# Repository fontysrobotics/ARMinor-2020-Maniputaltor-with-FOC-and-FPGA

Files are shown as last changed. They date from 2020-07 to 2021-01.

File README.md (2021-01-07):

# Affordable Manipulator With FPGA-driven FOC 

### Introduction 

Robotics can be prohibitively expensive and complex, preventing robotics students from learning about them. The goal of this project was to design an affordable, easy to use robot arm that would help solve these problems. The project was split into four parts: the electrical design, the mechanical design, the Field Oriented Control (FOC) implementation, and the simulation. Each of these projects' parts will be discussed in order below.

**This repository supports trainings at the ROS-Industrial training centre at Fontys University of Applied Sciences for the Adaptive Robotics minor ([ROSIN EP FREROS project](https://www.rosin-project.eu/ftp/freros))**

**This Educational Project has received funding from the European Union's Horizon 2020 research and innovation programme under the project ROSIN with the grant agreement No 732287.**



### Project structure

- **Electrical Design:** Within this folder you will find schematics, hardware documentation that was selected for the affordable manipulator.

- **Mechanical Design:** Within this folder you will find the proof of concept of the manipulator's mechanical design, alongside some design hardware selection documentation.

- **FieldOrientedControl:** Within this folder you will find the FOC implementation within FPGA boards. The files there is a simulink model of the controller and motors.

- **Simulation:** Within this folder you will find the simulation of the affordable manipulator in Unity. The project files for the communication between ROS and Unity, and the proof of concept of an GUI to interface with the simulation. 

**There is a final report available in this repository, which is meant to be the compiled version of our results and findings**

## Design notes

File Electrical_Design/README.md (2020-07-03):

# Electrical Design
## General information 
The robotic arm will have 6 axes with a 100W 3-phase ac motor in each. 
It has to have a tool interface at its end with a 24V power supply and 24V I/O pins.
The robotic arm should be able to be plugged into the 230V 50Hz mains. 

## Power supplies
For the main power supplies a MEAN WELL RSP-750-48 and a MEAN WELL RS-35-5 were chosen for the 48V and 5V lines respectively.
They fit all the requirements for safety features and the RSP-750-48 also has active power factor correction.
It can continuously deliver 750 W and has active cooling.
Thus, it would be able to power the motor drivers for extended periods of time. 
Unfortunately, something that cannot be remotely tested or calculated is how well it behaves with the transient load of the motors. 

The low voltage power supply can deliver up to 35W, which would be enough for all the systems that use 5V or less. Moreover, those systems do not cause the same problems with transient loads so the power supply will handle it well.

It should be physically tested whether the power supply witll be able to handle the transient load of the 6 motors turning on or off at once. 

## FPGA 
Because each motor controller board has an individual FPGA, an FPGA with less pins and less logic gates could be chosen.
The Spartan-3A Xilinx XC3S50A-4VQG100C (Xilinx) was a suitable choice because of multiple reasons.
Fist it got a suitable price for the goal.
It also has a package with pins on the side instead of a ball grid array.
This makes it much easier to solder it by hand, which is helpful for this in-house project.
Moreover, it is from Xilinx, which was already used previously in the minor, thus the students were already familiar with its software. 

## Tool power supply 
The tool power supply is a simple implementation of a Buck convertert that steps down the 48V for the power supply to 24V.
The design goal was to be able to provide at least 600mA current, but this one can go to over 1A.

## The schematic 
The schematic was done on the free version of Eagle 9.1.3. It was not build and physically tested.
Because of the corona outbreak it was not possible to go to Fontys and build or test anything physical.
Therefore it is reccommended that the schematic is first built on a prototype board and tested carefully. 

## Communication between the main controller and motor controllers
In order to minimize the amount of cables inside the robot arm the motor drivers will be inside the axes, next to the motors and the main controller will communicate with them through the I2C protocol.
In this way there will be only 5 cables that run through the arm, moreover the signal will be more noise proof compared to the situation where the motor drivers will be inside the base and the connection from them to the motors will run through the robot arm. 
The tool I/O will also be controlled through the I2C lines.
This is possible since the tool does not require a big I/O bandwidth and the I2C standard bandwidth will be fast enough to accommodate both all of the motor controllers and the tool I/O as well.

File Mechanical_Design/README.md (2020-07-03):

# Mechanical Design
For the mechanical design, there were two main parts that were considered:

The manipulator frame:

Aluminium extrusion was hosen for the frame, as this is lightweight, easy to acquire and assemble, and allows for the cables to be hidden.

The manipulator joints:

For the manipulator joints, pre-built joints were found.
These allow minimisation of cost and omplexity, while achieving high performance.

For more details on the components selected and he recommendations, please see the project report.

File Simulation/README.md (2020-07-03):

# Simulation

### Within this folder you will find two different project folders
- **GUI**: UR like interface proof on concept designed to interface with the simulation 
- **Simulation:** Robotic arm simulation in Unity

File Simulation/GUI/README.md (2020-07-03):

# ManArm Controller
## Description
This is a controller for a robot that had to be built during an Adaptive Robotics minor
at Fontys University of Applied Sciences.

Goals: 
* Provide a control interface similar to other robot arms on the market
* Support Linux including ARM, optionally windows  
* Save and load robot programs between platforms
* Control of each individual joint and IO pins

This project uses Tkinter as it supports different architectures. This toolkit is beginner friendly 
but also offers advanced features. 

## How to start
In order to start the UI you need to start the main_window.py with python 2. 

`` python src/gui/main_window.py ``

To run the guy you need to have `pillow` and `rospy` installed. You can install pillow by running.
`` pip install pillow ``

To install rospy please refer to installation of ROS. 

To run the unity simulation refer to the Simulation folder in this repository.

## Work in progress
This project is still in the early stage of development.

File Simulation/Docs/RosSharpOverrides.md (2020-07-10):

RosSharp Asset override list
======

| File | Changes |
|---|---|
| __Joint overrides__ | base joint management |
| `UrdfJoint` | Allowed the `Start()` function to be overridden |
| `UrdfJointRevolute` | - Added an encoder type system to track the angle of the joint as the build-in angle reporting is not always correct. <br /> - Added methods for motor control (velocity and effort control) |
| __Ros bridging__ | Overrides in message handling |
| `JointStateReader` | - Added calibration system so the zero angle can be changed / properly set. <br /> - Added normalization so values are between -180 and 180 degrees |

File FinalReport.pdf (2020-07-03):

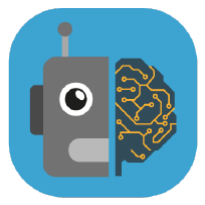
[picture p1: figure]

Fontys University of Applied Sciences

# Affordable Manipulator With FPGA-driven FOC

Final progress report

7-1-2020

Limpens, Jordie J.J.N.
Marinov, Mihail M.M.
Mindiola Romero, Ray R.D.
Sminia, Sean, S.M.
Strik, Leonardo L.S.

I
Affordable Manipulator With FPGA-driven FOC - Preface

## Preface

This document is the final report of a project about the design of an affordable 6 degree of freedom manipulator arm, which was part of the Adaptive Robotics minor at Fontys University of Applied Sciences. The goal of the project was to design an affordable robot arm, that could be used for educational purposes. It was motivated by the fact that currently available robot manipulators are expensive and although Fontys has a few, close to project deadlines the demand for them is too big. An affordable, in-house produced manipulator arm would not only help meet the student’s demand, but, since students will have access to the design documents and source code, will also allow them to improve it and modify it while studying robotics.

The project was worked on in the period from March 2020 until June 2020. Unfortunately, the project coincided with a global pandemic, which caused all work on the project to be remote, thus nothing could be physically made nor tested. This limitation has shifted the initially planned goals and end product of the project. Despite the difficult period, the group has put effort in order to finish as much as possible in order to provide a solid groundwork for the completion of
the initially intended product.

The group members would like to express significant appreciation to Peter Klijn, who was our tutor for this project and helped us greatly. We also are thankful to Pablo Negrete, who created the project, gave us tips and acted as a client for the project’s purposes. We are thankful for the advice given by Esmaeil Najafi, which was also very helpful for our project. Lastly, we also wish to acknowledge the help provided by Edwin Insuasty from MathWorks with modelling and designing the motor controllers of the robot arm.

This report is mainly intended for the students who will continue working on this project, as well as the teachers who will assess our work. The document is divided into different chapters for different fields of engineering in order to facilitate finding the information that the reader is seeking. In the end recommendations for further development are listed.

II
Affordable Manipulator With FPGA-driven FOC - Contact details

## Contact details

Below, the contact details for all group members, the client, and the tutor are presented.

### Group members:

Name | Student number | Email | Phone number
Ray Mindiola | 2588005 | r.mindiolaromero@student.fontys.nl | +31 6 49 674 116
Sean Sminia | 2718383 | s.sminia@student.fontys.nl | +31 6 29 027 316
Leonardo Strik | 2909332 | l.leonardo@student.fontys.nl | +31 6 36 348 027
Mihail Marinov | 3225666 | m.marinov@student.fontys.nl | +31 6 40 901 311
Jordie Limpens | 3312976 | j.limpens@student.fontys.nl | +31 6 27 122 022

### Client:

Name | Pablo Negrete Rubio
Email | p.negreterubio@fontys.nl
Phone number | 0885074731

### Tutor:

Name | Peter Klijn
Email | p.klijn@fontys.nl
Phone Number | 0885070657

III
Affordable Manipulator With FPGA-driven FOC - Summary

## Summary

Robotics can be prohibitively expensive and complex, preventing robotics students from learning about them. The goal of this project was to design an affordable, easy to use robot arm that would help solve these problems. The project was split into four parts: the electrical design, the mechanical design, the Field Oriented Control (FOC) implementation, and the simulation. Each of these projects' parts will be discussed in order below. For the electoral design, there were three main decisions: Using two different power supplies, a low and high voltage one, to eliminate interplay , the use of separate FPGA drivers for each motor, to minimize interference and cables through the arm, and the application of the I2C protocol to communicate sensor and motor data. In regard to the mechanical design, there were two important decisions: The use of aluminium extrusion, to minimize weight and complexity, and the application of pre-built joints, to minimise cost and complexity. The FOC implementation within Simulink and the exported VHDL code seemed to behave accordingly, although sufficient testing lacked due to time constraints. In order to minimize complexity and cost, pre-configured full system kits were chosen for the FOC solution. In regard to the simulation, Unity was chosen as a simulator. The interfacing between ROS and Unity is done through ROS Bridge and ROS Sharp. Joint state control and readout has largely been implemented, although only a few sensors are. The user interface for the control of the robot was implemented in the ‘TKinter’ Python framework, because of its cross-platform applicability. In general, most parts of the problem were delayed due to the circumstances, and therefore this document should mostly be used to guide future design, rather than as a full-fledged design document.

IV
Affordable Manipulator With FPGA-driven FOC - Table of contents

## Table of contents

V
Affordable Manipulator With FPGA-driven FOC - Table of contents

VI
Affordable Manipulator With FPGA-driven FOC - Table of figures

## Table of figures

Figure 1: V-model illustration, taken from (RMS, 2017) | 3
Figure 2: SCRUM method illustration, taken from (Gonçalves, 2018) | 4
Figure 3 Motor Drivers | 7
Figure 4 ADC | 8
Figure 5 Motor Encoders connectors | 8
Figure 6 Negative voltage generator | 9
Figure 7 JTAG interface | 9
Figure 8 Part of power supply | 10
Figure 9 Tool power supply | 10
Figure 10: An early-stage concept design for the manipulator. The individual degrees of freedom are
marked and numbered | 12
Figure 11: The aluminium extrusion which was chosen for the manipulator arm | 13
Figure 12: the robolink D high-end robotic joint size 30 from igus (igus) | 13
Figure 13 - FOC model structure | 15
Figure 14 - Input block | 15
Figure 15 - FOC subsystem | 16
Figure 16 - FOC block | 16
Figure 17- PWM Generator block | 17
Figure 18: Motor Subsystem | 17 (https://stichtingfontys.sharepoint.com/sites/armProjectTeam/Gedeelde%20documenten/General/FinalReport.docx)
Figure 19: Motor speed (blue) compared to the target speed (yellow). Y axis is RPM, X axis is time. A
load is added at 0.5 seconds | 18
Figure 20 MC58420 from Magellan (Performance Motion Devices, Inc., n.d.) | 19
Figure 21: TMC4671-ES from Trinamics. (Trinamic, n.d.) | 20
Figure 22: An integrated FOC motor control board by Odrive | 20
Figure 23 EVALKIT-ROBOT-1 from STMicroelectronics (STMicroelectronics, n.d.) | 21
Figure 24: Architectural overview of the ROS communication structure | 23
Figure 25: A picture of the GUI. On the left are the joint controls, and on the right the manipulator
visuaisation | 25 (https://stichtingfontys.sharepoint.com/sites/armProjectTeam/Gedeelde%20documenten/General/FinalReport.docx)
Figure 26: Velocity controller block inside the FOC subsystem | 32
Figure 27: Current controller block inside FOC subsystem | 32

## Table of tables

Table 1: The additional requirements for the design | 14
Table 2: FOC Solution comparison table | 21
Table 3: The table of requirements, split into ROS, Cost, Safety, Size, Production and Design
requirements | 31

Affordable Manipulator With FPGA-driven FOC - Introduction

## 1. Introduction

Robotics is an ever-growing field of education, where many students learn valuable technological skills. However, this type of education can be gated by the high cost of robotic platforms, which allows only few of these units to be purchased. This has been experienced by the project group in their own minor, where gripper model testing was greatly complicated by the small number of available arms. Furthermore, robot platforms can be complex and closed source, preventing students from learning more about their inner workings.

As part of the minor Adaptive Robotics, and in cooperation with Pablo Negrete Rubio, a project was formed, with the intent of solving these problems. Pablo expressed his desire for a small form factor robotic manipulator arm that could be mounted on mobile platforms. With the intent of making the arm ROS compliant integration with mobile platforms should be made easy.

As this project is part of the adaptive robotics minor, the project length is set to end on the 3rd of July, 2020. The deliverables of the project include this report with its design files and an ending presentation as well as a prototype. Further Two specific learning goals were set by Pablo, FOC drive and ROS compliance. These learning goals were written as must in the requirements list. In order to achieve a functional prototype, and maintain as low a price-point as possible, pre-manufactured components are used, instead of designing parts from scratch.

Besides the design the scope of the project is important. The design was envisioned to be portable and to be used by students and researchers. This gives a different design philosophy as functionality and technical documentation becomes more important. Matters such as marketability and designing for specific use-cases is outside the scope of this project. This includes not creating variants or investigating certifications at this point in time.

Due to the impact of the Corona virus regular operation could not continue. For the project this meant not having physical access to the Fontys building or supplies. Therefore, the project deliverables were altered to a virtual prototype in the form of a simulation and the design and validation files being changed to design and recommendations. In this document each component of the design has its own recommendation as to why it was selected but no physical tests associated with it. The simulation is the only section in which a test case was tested.

The limitations of working from home and having everything being virtual have presented challenges. It has also prevented a lot of testing and has allowed for little progress into researching production as well as user interaction. While a design could be made from the recommendations alone, thorough scrutiny should be applied as the lack of physical interaction might have influenced the design.

Affordable Manipulator With FPGA-driven FOC - Introduction

### 1.1. Report reading guide

The information within the report will be structured in the following manner:

- The first chapter, introduction, contains background information surrounding the project, defines the project scope of the project.
- The second chapter, project description, contains the goals of the project, the projected use case, defines the requirements of the project and describes the organization techniques used in the project.
- The third chapter, electrical design, addresses the electrical design decisions of the affordable manipulator arm. It contains the progress achieved in the project regarding this area of the project, including some recommendations on how to continue with the design.
- The fourth chapter, mechanical design, addresses the electrical design of the affordable manipulator arm. It contains the progress achieved in the mechanical aspect of the affordable manipulator arm. Includes hardware choice suggestions for the future.
- The fifth chapter, field-oriented control implementation, goes over the experimental approach taken to introducing an FOC into an FPGA. It goes into detail on the approach used to accomplish the task. It also goes over possible, comparable alternatives that should be considered.
- The sixth chapter, simulation, contains the progress pertaining the simulation of the project. Including choice of environment, communication with ROS (Robot Operating System) and it addresses the progress made creating a graphical user interface for this simulation.
- The seventh chapter, conclusion, contains the results achieved in the project.
- The eighth chapter, recommendation, contains all the points of interest for the improvement of the results achieved and for the continuation of the project in the near future.

Affordable Manipulator With FPGA-driven FOC - Project description:

## 2. Project description:

This chapter will contain all relevant details about the minor project, including the vision for the project and the project approach and organization. This first part of the chapter will go over the goals of the project. The second section will describe the use case of the project. In the third section, the requirements drawn will be presented. In the fourth and final section of this chapter, the planning and organization of the project are overviewed.

### 2.1. Project goals

The ultimate goal of the project is to create a design for a miniature robotic manipulator, upholding an interest of keeping the cost of production as low as possible. The creation of such design would then be applied for the education sector, targeting specifically students and researchers, for them to freely experiment and work with robotic arms without concerns of availability in the future.

The design recommendations produced by the project will be evaluated and analysed, creating future project opportunities for the affordable manipulator to fully come into fruition.

### 2.2. Use case

The projected use case would be that of a miniature robotic arm, which should interface with ROS (Robot Operating System) or directly into its control board. Where it can be used in a similar manner as to a Universal Robot series manipulator, with the ability to taken home with relative ease. It should be able to accomplish movement with 6 degrees of freedom.

### 2.3. Requirements

The full table of requirements can be found in Appendix 1. An important remark that must be kept in mind, is that these requirements were agreed upon with the intention of producing the final design. However, unfortunately, the world underestimated the severity of the global pandemic caused by the coronavirus. This had severe consequences on what was able to be accomplished by the project group, and as such, the scope of the project was ultimately reduced to the design of the arm.

### 2.4. Organization

During this project, a combination of the V-model and SCRUM method was used. The V-model is an abstract model of the system development lifecycle. The V-model is split on two sides: the left side of the V-model systematically outlines the user requirements and system design; at the neutral bottom point lies the integration of the system; the right side focuses in the verification and testing of the project. An illustration of the V-model can be found in Figure X.

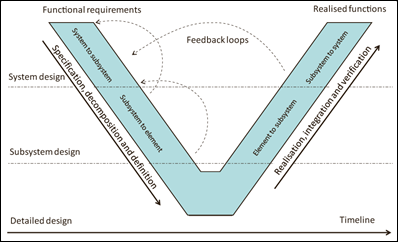
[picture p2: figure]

Figure 1: V-model illustration, taken from (RMS, 2017).

Affordable Manipulator With FPGA-driven FOC - Project description:

Upon agreement and request of the client, the SCRUM method was chosen. The SCRUM method splits the whole assignment into small, timed sets of tasks called “sprints”. There are small meetings at the end of the sprint deadlines to check progress and discuss results achieved within those sprints. Within the following figure, an illustration of the SCRUM method can be found.

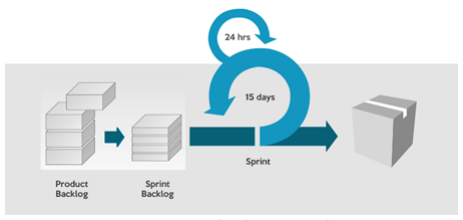
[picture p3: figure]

Figure 2: SCRUM method illustration, taken from (Gonçalves, 2018). .

The use of these tools proved themselves invaluably useful when faced against the current world situation. It allowed the team members to stay well in touch with each other and allowed an appropriate handling of the oncoming issues and challenges that would have been otherwise difficult to address given the current global pandemic crisis.

Affordable Manipulator With FPGA-driven FOC - Electrical design

## 3. Electrical design

The robot arm is a machine with specific power supply requirements. The problem comes not from the high-power consumption, but from the fact that motors instantaneously switch from requiring zero power to requiring hundreds of watts, and vice versa. In this case there are six 100-Watt motors which should be able to move at once. Moreover, there are also components which use a lower voltage rail such as the motor controllers or main microcontroller. This low-level voltage line must be stable regardless of the motor’s usage in order to keep the robot arm safe and precise.

The manipulator is designed to be interchangeable with the Universal Robots UR5 for tool interfacing. In other words, the manipulator should have the same tool power supply and logic voltage levels. The robot must be able to use the normal power grid and be plugged into a normal power socket and it must also adhere to the current electrical safety standards.

The 6 motors will cause EMI and therefore the robot’s electrical systems should be designed to be able to withstand noisy environments.

### 3.1. Requirements

- The robot must use the standard 230V 50Hz power grid.
- The robot must feature safety system for short circuit, overload, over voltage, over temperature, EMC protection
- The power supply must have power factor correction
- The power supply should be able to continuously deliver power to 6 x 100 W motors.
- The low-level voltage rail should be independent from the high-level voltage line
- The tool power supply should provide 24V and at least 600mA current
- The tool I/O must use 24V
- The communication with the main controller and other systems should be able to withstand EMI
- Cables should fully fit inside the arm, with no outside connections.

### 3.2. Design decisions

Because of the requirement for a stable low voltage line and the fact that the high voltage rail might become unstable when motors start or stop it was decided to use 2 separate power supplies. The low voltage line will be 5V and the high level one will be 48V.

In order to minimize the amount of cables inside the robot arm the motor drivers will be inside the axes, next to the motors and the main controller will communicate with them through the I2C protocol. In this way there will be only 5 cables that run through the arm, moreover the signal will be more noise resistant compared to the situation where the motor drivers will be inside the base and the connection from them to the motors will run through the robot arm.

The tool I/O will also be controlled through the I2C lines. This is possible since the tool does not require a big I/O bandwidth and the I2C standard bandwidth will be fast enough to accommodate both all of the motor controllers and the tool I/O as well. The tool power supply will step down the 48V voltage line to 24V using a switching mode DC/DC converter as it would be more power efficient compared to the other option of using a linear power regulator.

A requirement of the project was to implement the field-oriented motor control on an FPGA. There were two options to achieve that. Either there had to be one or multiple FPGAs in the base of the robot or each motor controller had to have a separate FPGA. The problem with the first approach was that the amount of wires necessary to connect from the motor controller board to the FPGA will

Affordable Manipulator With FPGA-driven FOC - Electrical design

be so big, that it would be impossible to fit all the cables for the 6 motors together inside the arm. The option to use some communication protocol for communication with the motor controller boards through less cables would have been unfeasible as it would require things to be send sequentially which would eliminate the whole point of using an FPGA. Therefore, the approach with an FPGA per motor controller was chosen.

### 3.3. Hardware components

For the main power supplies a MEAN WELL RSP-750-48 (Mean Well, 2019) and a MEAN WELL RS-35-5 (Mean Well, 2011) were chosen for the 48V and 5V lines respectively. They fit all the requirements for safety features and the RSP-750-48 also has active power factor correction. It can continuously deliver 750 W and has active cooling. Thus, it would be able to power the motor drivers for extended periods of time. Unfortunately, something that cannot be remotely tested or calculated is how well it behaves with the transient load of the motors.

The low voltage power supply can deliver up to 35W, which would be enough for all the systems that use 5V or less. Moreover, those systems do not cause the same problems with transient loads so the power supply will handle it well.

Because each motor controller board has an individual FPGA, an FPGA with less pins and less logic gates could be chosen. The Spartan-3A Xilinx XC3S50A-4VQG100C (Xilinx) was a suitable choice because of multiple reasons. Fist it got a suitable price for the goal. It also has a package with pins on the side instead of a ball grid array. This makes it much easier to solder it by hand, which is helpful for this in-house project. Moreover, it is from Xilinx, which was already used previously in the minor, thus the students were already familiar with its software.

The ADC is ADC0820BCN (TI), it was chosen because it has a suitable package and it can measure as much as 400kSPS, which is enough for the FOC motor controller.

The OpAmps used for conditioning the current for the ADC are MCP602SN. They are SMD, cheap, work with a 5V power supply and have a good bandwidth and voltage slew rate for the purpose (MCP602SN datasheet).

The power MOSFETs are BUZ10 (ST), they have a suitable power dissipation, maximum current, maximum drain source voltage, maximum gate source voltage and are of a suitable price.

### 3.4. Schematic design

Because the free version of EAGLE does not allow designs with more than 2 sheets of a single schematic the schematic snippets will be cut from the big schematic.

Affordable Manipulator With FPGA-driven FOC - Electrical design

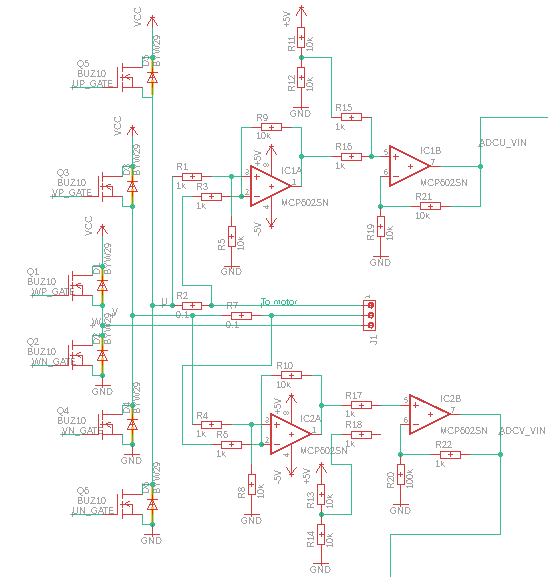
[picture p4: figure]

Figure 3 Motor Drivers

The motor drivers (Figure 3 Motor Drivers) use a standard architecture for controlling 3 phase AC motors. There are also 2 current sensing resistors (R2, R7). The voltage over them is measured by the first OpAmp and then it is added to 2.5V and amplified to better fit in the 0 – 5V range of the ADC.

Affordable Manipulator With FPGA-driven FOC - Electrical design

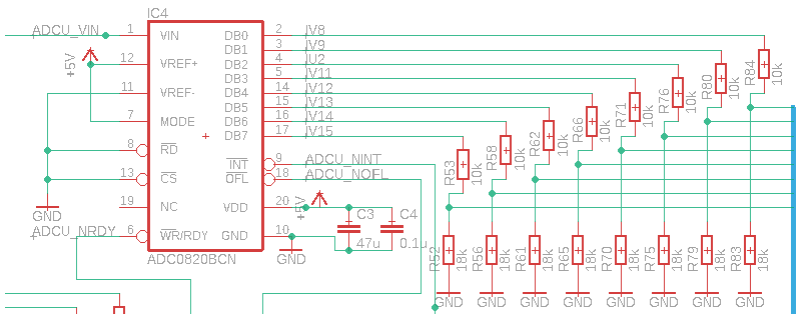
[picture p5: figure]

Figure 4 ADC

The ADC (Figure 4 ADC) uses 5V logic levels, so it is necessary to step down the voltage from 5V to 3.3V so that it can be read on the FPGA. This can be done either by an integrated logic level shifter, but in this case, it wasn’t necessary to do bidirectional voltage level transfer. On the bright side, the ADC accepts any signals higher than 1.8V as a logical high so shifting the voltage the other way around is not necessary. On the other hand, this is currently not necessary as in this configuration the ADC measures automatically all the time, so there is no data going from the FPGA to the ADC.

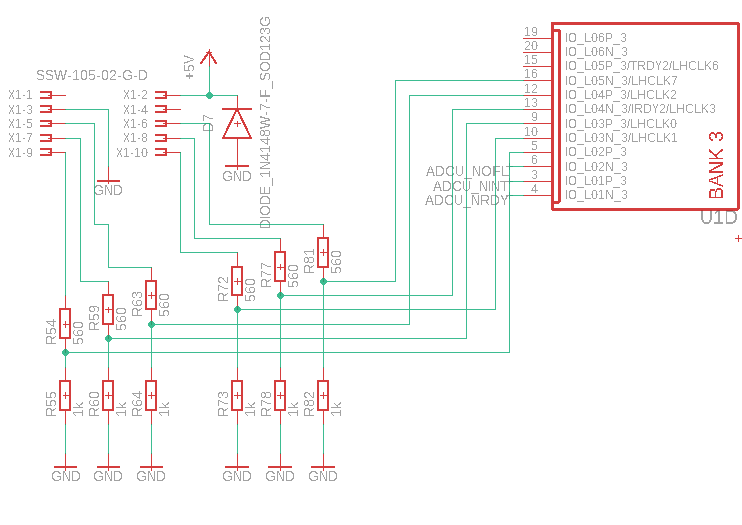
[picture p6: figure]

Figure 5 Motor Encoders connectors

Affordable Manipulator With FPGA-driven FOC - Electrical design

Another component that attaches to the FPGA are the motor encoders (Figure 5 Motor Encoders connectors). They also work on 5V, so the same voltage level shift is necessary. For the same reason that the data in unidirectional, it is easier to use resistor voltage dividers instead of an integrated voltage level shifter.

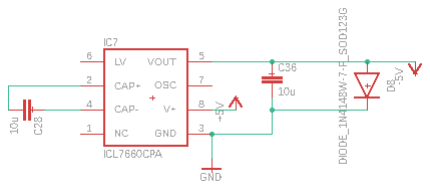
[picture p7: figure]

Figure 6 Negative voltage generator

This negative voltage generator (Figure 6 Negative voltage generator) is necessary to measure the voltage over the current sensing resistor for the motor current.

There is also the JTAG interface for programming the FPGA (Figure 7 JTAG interface). It attaches to an external programmer so that the FPGA can be programmed while in circuit. There is also an indicator LED, to show when the FPGA is ready.

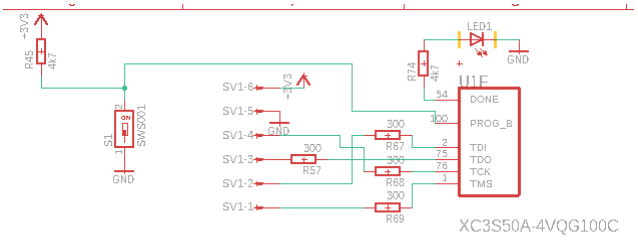
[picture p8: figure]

Figure 7 JTAG interface

The last thing is the power supply for the FPGA (Figure 8 Part of power supply). It can use different power supplies for each I/O bank, but in this design, this is not necessary as all the lines use 3.3V. The core of the FPGA uses 1.2V which was also done using a linear voltage regulator. There are numerous capacitors in order to make the voltage line stable and remove harmonics. The capacitors were used based on the design of the development board of the same FPGA (Xilinx, 2007). There are also 2 similar configurations on the left of the U2G block but were not included in the screenshot for

Affordable Manipulator With FPGA-driven FOC - Electrical design

readability.

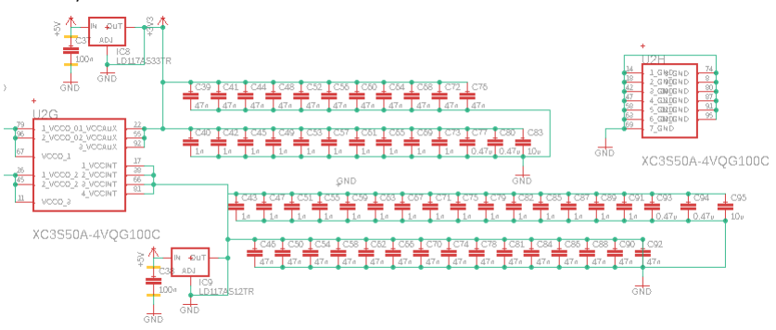
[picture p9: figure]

Figure 8 Part of power supply

The tool power supply (Figure 9 Tool power supply) uses a buck converter to step down the voltage. This design actually allows currents higher than the one that the UR5 uses, but a higher maximum than the requirement is not a problem. So this design is feasible.

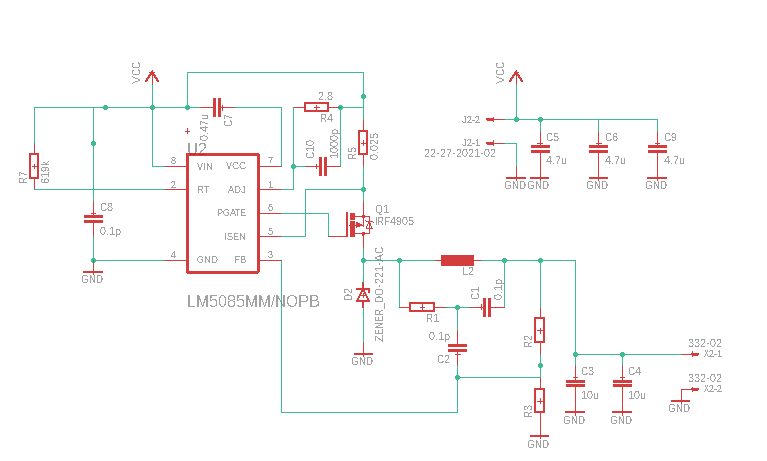
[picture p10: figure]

Figure 9 Tool power supply

### 3.5. Future steps

First and foremost, the circuit board must be built as a prototype and tested, whether all voltage levels are as expected.

When the circuit board is verified to behave as expected, a test script should be made, to start the motors and move them with full power before stopping again in order to monitor if the power rails are stable during usage. If that is not the case either the motor control algorithm should be changed

Affordable Manipulator With FPGA-driven FOC - Electrical design

in order to make the motor startup more gradual, or additional capacitors can be added in the robot base, if the power line is unstable, but still very close to being within limits.

The board layout is not done, as this depends a lot on the real-life test of the circuit board. For example, if the motor driver MOSFETs get very hot, a heat sink should be integrated, or the MOSFETs can be thermally coupled to the case of the robot arm in order to spread the heat over a bigger area. The temperature of the other components should be also monitored.

To make the board layout compact, but still serviceable in Fontys 1206 SMD capacitors and resistors are best to be used. They are a good compromise between space, and serviceability. Not all components can be SMD, as some of the capacitors for the power supply cannot be found in an SMD package.

The 48V power cables that run inside the arm should have a core area of at least 4mm²
to cope with
the continuous current if the motors are continuously on.

The tool I/O has to be finished because of time constraints it was not been done. It can be either done using a small microcontroller to set latches and read inputs. Another option is to use an already done GPIO I2C controlled expansion board. In both cases the voltage level will have to be shifted, to and from 24V.

Affordable Manipulator With FPGA-driven FOC - Mechanical design

## 4. Mechanical design

This chapter will detail the mechanical design. Unfortunately, due to time constraints, the mechanical design was not finished. The choices and design decisions that were made will be detailed below.

Of the set requirements, those that were relevant during the mechanical design are those concerning the payload weight, size and production of the arm. The arm can be no longer than 710 mm, must be able to take a payload of 200 grams, and must be able to be produced relatively simply, for less than € 1500 in larger numbers. A concept design for the manipulator is shown in Figure 10. This figure also shows the degrees of freedom. Also shown in the concept model is the base, the size of which is not definite yet, due to some uncertainty on the electrical front. However, a base with some cooling facilities needs to be included in the design.

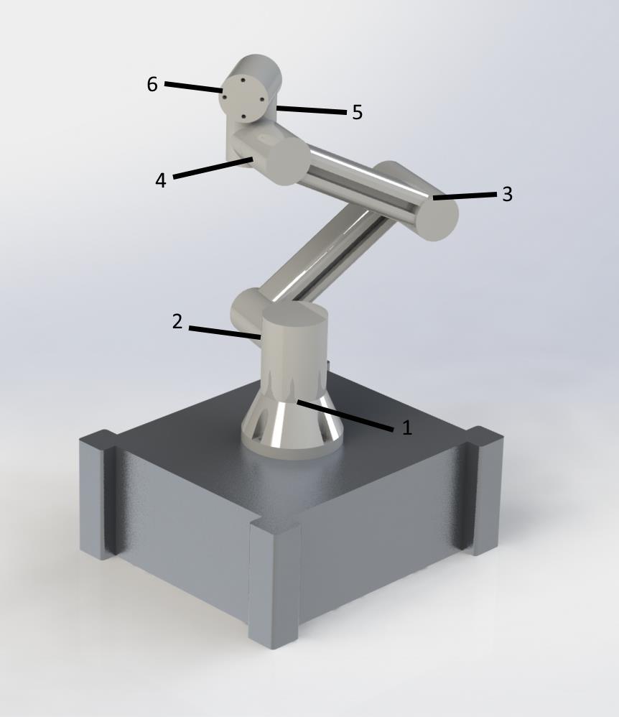
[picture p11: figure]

Figure 10: An early-stage concept design for the manipulator. The individual degrees of freedom are marked and numbered.

Affordable Manipulator With FPGA-driven FOC - Mechanical design

### 4.1. Manipulator frame

The material chosen for the manipulator arm itself is aluminium extrusion, specifically a 50*50 mm type 2E L one, shown in Figure 11. This allows for simple assembly of the manipulator, and is readily available for a low price. This profile also has covered channels running through it, which allows the cables to be hidden, as per the requirement, and helps prevent electromagnetic interference.

Figure 11: The aluminium extrusion which was chosen for the manipulator arm.

### 4.2. Manipulator joints

During the design process, the design of the joints quickly proved to be the most challenging. The fact that the cables needed to be hidden means that the joints have to be able to have the cables pass through them. This means that the bearings required have to be extremely large, and therefore costly, upwards of €150. Secondly, the high motor speeds requires significant reduction. In order to prevent motor backdriving and achieve this reduction, a worm gear redactor was chosen. Sourcing worm gear redactors proved that these, also, are relatively costly, and can cost upwards of €300 each. Since both of these components alone would cost upwards of €450 per joint, which would exceed the budget, a more affordable solution had to be found. To provide joints that satisfy the requirements at a reasonable cost, Igus robolink joints were found. The robolink D highend robotic joint size 30, which is shown in Figure 12 has a width of 45 mm (igus), which matches the aluminium extrusion, and is therefore the component that was chosen for the joints. These joints cost €288, which presumably could be lowered when scaling up production.

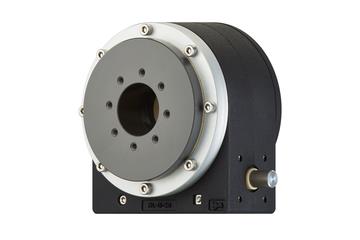
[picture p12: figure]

Figure 12: the robolink D high-end robotic joint size 30 from igus (igus).

Affordable Manipulator With FPGA-driven FOC - Mechanical design

### 4.3. Mechanical design requirements

In order to aid further mechanical design, the recommendations that result from this project are summarized as a set of requirements, which can be used in addition to the main project requirements in the plan of approach. These requirements are categorized in Must, Could, Should and Would requirements, and can be found in Table 1.

Table 1: The additional requirements for the design.

Nr. | Requirement | MSCW
1 A hollow base to house the electrical components such as power supplies and | circuit boards, with adequate cooling must be provided. | M
2 | The base should be weighted enough to offset the arm plus payload. | M
3 Complete pre-fabricated robot joints should be used in order to minimise | production cost and complexity. | S
5 The possibility of using different motors and joints for different degrees of freedom, | according to the load. This would minimise cost. | S
5 In order to allow the cables to be hidden in the arm, and minimise weight, the arm | segments should be hollow. | S
6 In order to allow the cables to pass through the joints, bearing with a large enough | inner diameter should be used. | S

Affordable Manipulator With FPGA-driven FOC - Field Oriented Control implementation

## 5. Field Oriented Control implementation

The project requirements include the implementation of an FOC within a FPGA board to achieve the control of smaller, yet still powerful motors, to be used in the design of the arm. In order to do so, it was decided that a using Xilinx Vivado would present multiple obstacles in the future of the project; specifically, in regards to complex functions such as the Park transform, and the inverse Park transform. As an alternative, MATLAB Simulink models can be exported to HDL, which then in turn, can be synthesised within FPGAs. This method was chosen for the project, because of the flexibility to tune the model to motor specifications and controller requirements it offers.

### 5.1. Structure of the FOC model:

The model, which is shown in Figure 13, is divided into subsystems to simplify the process of modifying the model, and make it clearer to understand, for the continuation of the project in the future. As it stands, the current model is divided into 4 subsystems: Input, FOC, Motor and Visualization.

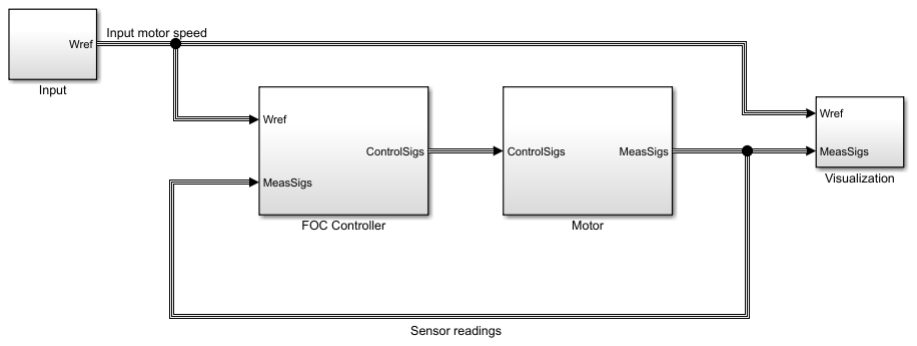
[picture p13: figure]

Figure 13 - FOC model structure

Below, a brief overview of each block and its functions will be given:

5.1.I.The input:
The input subsystem, shown in Figure 14, contains the generation of the input for the model, which is the desired rpm of the motor. This value is then transformed into radians per second (rad/s) before being exported out of the block.

Figure 14 - Input block

Affordable Manipulator With FPGA-driven FOC - Field Oriented Control implementation

5.1.II.The FOC:
The FOC subsystem is further divided for clarity, it is comprised of the input speed block and sensor block, which decouples the input signals and sends them to the FOC block. the motor signal generation, which acts as a PWM generator, taking the control signal from the FOC and transforming it into voltages for the motors. This is visualized in Figure 15.

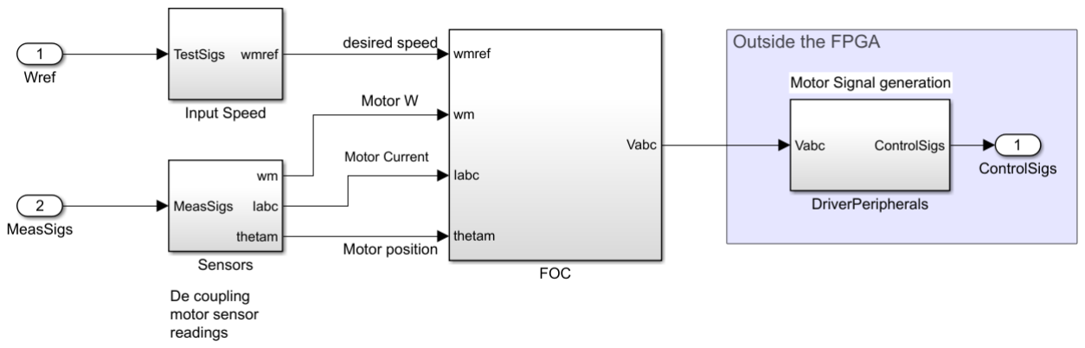
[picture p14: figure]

Figure 15 - FOC subsystem

Inside the FOC block, the desired speed and measured speed are taken into a standard PI controller, which can be seen in Appendix 2, the control signal output of the velocity PI is then used as a reference for the current controller. The current controller uses PI controllers for the current components given from the Park Transform (Id and Iq), which can be seen in Appendix 2. The FOC block can be seen in Figure 16.

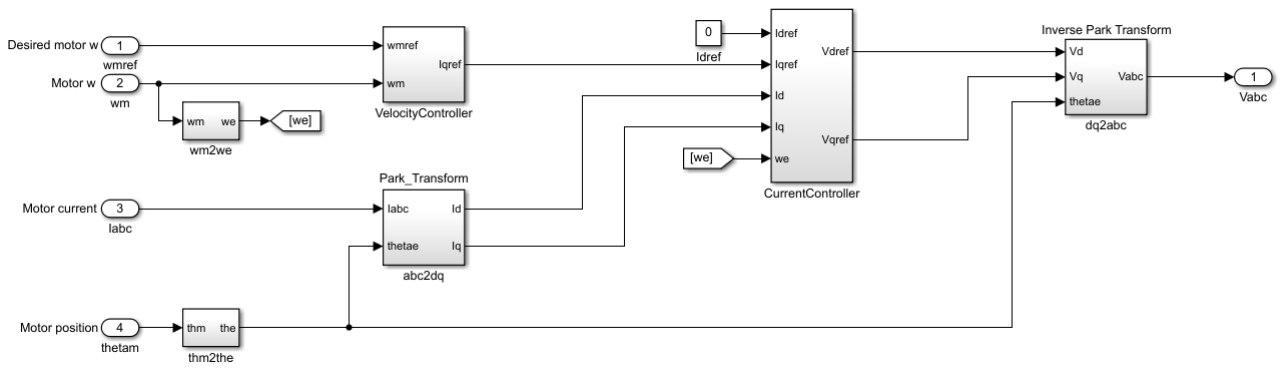
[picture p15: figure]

Figure 16 - FOC block

Affordable Manipulator With FPGA-driven FOC - Field Oriented Control implementation

The output signal from the FOC is taken into the PWM generator, which outputs 6 gate signals for the control of the motor. This part of the model is external to the FPGA and the output is directly connected to the motor subsystem. It is illustrated in Figure 17.

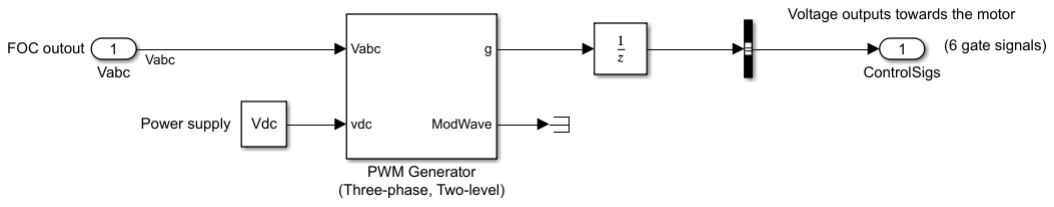
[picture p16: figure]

Figure 17- PWM Generator block

5.1.III.The motor:
The motor subsystem, shown in Figure 18, is comprised of a modelled inverter, which represents a circuit of six Insulated-gate bipolar transistors (IGBT) to convert the control gate signals from the FOC into the Phase voltages for the motors. The current and phase voltages are measured, and the current measurements are used for the controller. The motor block has been modelled as a permanent magnet synchronous motor. The parameters of the modelled motor have been adjusted to match the selected motor as closely as possible. Finally, there is a sensor that measures the motor position, speed, and torque, and a load attached to the motor to verify the integrity of subsystem.

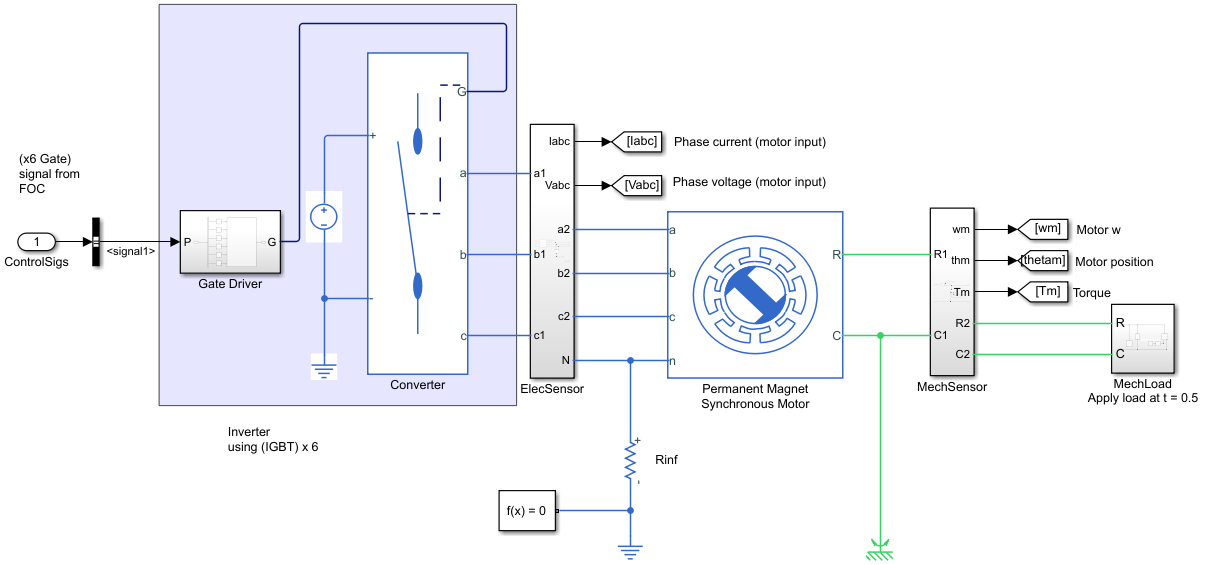
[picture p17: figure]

Figure 18: Motor Subsystem.

Affordable Manipulator With FPGA-driven FOC - Field Oriented Control implementation

### 5.2. Variable input for the model:

Attached to the Simulink model file, is a MATLAB Script file which contains a list of simulation parameters that can be modified. In order to successfully run the simulation, it is required to run the parameter script file before the model file. In order to use the simulation file with another, similar motor, the values must be modified, and the controllers need to be tuned again.

The parameters required to be filled in should be found within the component datasheets and/or provided at request from the manufacturer.

### 5.3. Model limitations:

The model, as it stands, requires the tuning of three different PI controllers, which can be challenging. MATLAB Simulink’s auto tuner function cannot be used for this, as it is incompatible with the use of PWM signals and continuous time functions across the whole model.

It is possible to overcome this issue by using the System Identification toolbox (Mathworks, n.d.), to linearize the parts of the model that include the controllers. But the license for the toolbox was currently unavailable and due to time constraints, it was not able to be acquired in time.

Despite that, the model is able to behave as intended, but if changes need to be made to the parameters of the model, then the tuning of the controllers must be addressed. The motor model behaviour is shown in Figure 19

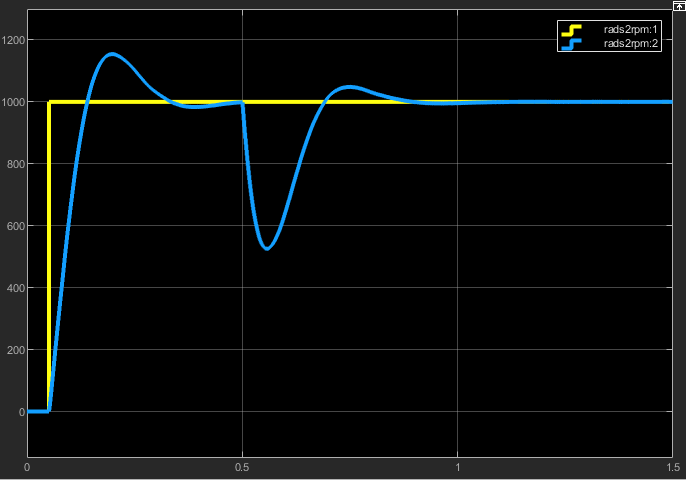
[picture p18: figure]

Figure 19: Motor speed (blue) compared to the target speed (yellow). Y axis is RPM, X axis is time. A load is added at 0.5 seconds.

Affordable Manipulator With FPGA-driven FOC - Field Oriented Control implementation

### 5.4. VHDL import:

The FOC block is able to be exported into VHDL, and the code successfully compiles on Xilinx’s Vivado software. Unfortunately, testing was not able to be performed due to lack of hardware and time constraints.

Given the current limitations of the approach taken in this project, it is advisable to also consider possible alternatives of FOC control that would lead into similar or more desirable results.

### 5.5. FOC alternative methods

There are Figure 20many alternative FOC solutions within the industry. Below is a brief description of several of these alternatives, along with their strengths and weaknesses. Below that is a comparison table that details on what criteria the method used in the project was chosen.

5.5.I.Logic IC and amplifier
Magellan’s MC58000 series offers solutions in the form of an Integrated Circuit (IC) that handles the FOC logic , paired with a digital amplifier to power the motors, shown in Figure 20. This system is highly configurable as both the logic type and its tuning can bet set separately from the power delivery. (Performance Motion Devices, Inc., n.d.) The digital amplifiers regulate both the input and output voltage and can even correct for wire losses. However, these systems are designed for highend use which is outside of the budget range for the project.

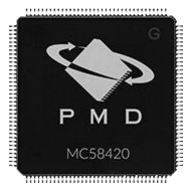
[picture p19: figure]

Figure 20 MC58420 from Magellan (Performance Motion Devices, Inc., n.d.)

Affordable Manipulator With FPGA-driven FOC - Field Oriented Control implementation

5.5.II.Power logic IC
Trinamics’s TMC4671 Series, shown in Figure 21, offers solutions for the smaller motors which the project requires (Trinamic, n.d.). It combines an amplifier and the FOC logic onto a single IC. Due to the size of the system it is only suited for small/ low-power motors. The ICs power input and output can be scaled to allow high power usage, the circuitry required for these changes can be found in the user guide provided by the manufacturer.

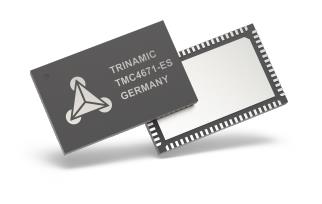
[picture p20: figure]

Figure 21: TMC4671-ES from Trinamics. (Trinamic, n.d.)

5.5.III.FOC control board
This option is a self-contained FOC motor control board. An example of one from Odrive is shown in Figure 22. These boards contain both a power circuit and a logic IC for the FOC calculations. These kinds of boards come pre-built and only require wiring to power it and connect the motor. These boards come in many variants. Boards vary in operating ranges, tune-ability, customization, frequency and more. Therefore, selection of the right control board to suit the motor is crucial in this case.

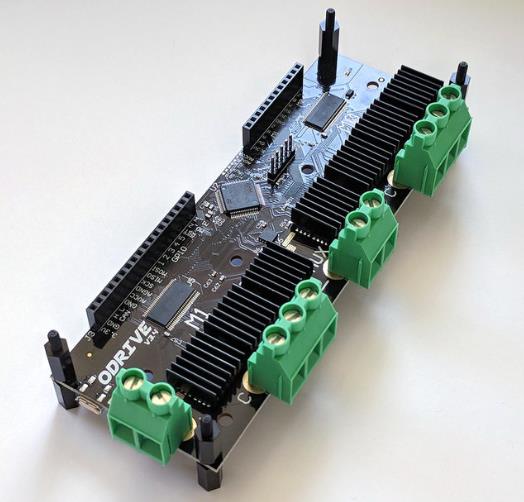
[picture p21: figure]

Figure 22: An integrated FOC motor control board by Odrive.

Affordable Manipulator With FPGA-driven FOC - Field Oriented Control implementation

5.5.IV.Full system
The difference between a full drive system and the above mentioned options is that the former includes a pre-selected motor. By having a pre-selected motor, the freedom of customization is compromised. This makes mass manufacturing easy and allows for a consistent product, that is easy to use. The biggest downside of this solution is the limitation of the packages. They are limited to a small range of motors and operating ranges. An example of this, would be the EVALKIT-ROBOT-1 from STMicroelectronics, which is illustrated in Figure 23. It is an evaluation kit that includes motor and board. The motor included in the kit is the same as the one selected for the design, making it perfectly compatible with the design produced.

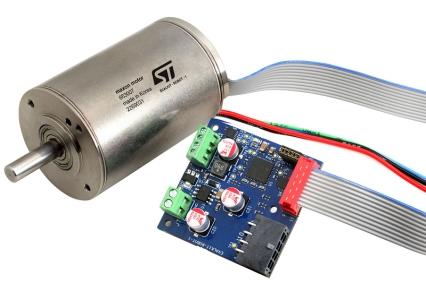
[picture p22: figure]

Figure 23 EVALKIT-ROBOT-1 from STMicroelectronics (STMicroelectronics, n.d.)

5.5.V.Advantages/disadvantages
To compare the different solutions, Several evaluation categories were created. Each category is then assigned an importance, in the form of a weight. It is assumed that motor specifications are available for each solution, and that each solution provides adequate levels of precision and torque, when making this comparison. Then, each option is ranked 1-4 on each category, where 1 is best and 4 is worst. These ranks are multiplied by the weight of their respective category, and added. The option with the lowest resulting score is the most preferable. To be clear, Tune-ability is the option to change the FOC behavior by tuning the internal PID. Configurability is the width of the margins for operation.

Table 2: FOC Solution comparison table.

Cost | Ease of use | Tune-ability | size | configurability Weighted scores
Weight | 3 | 3 | 1 | 2 | 1
Logic + amplifier | 4 | 3 | 2 | 4 | 1 | 32
Power Logic | 2 | 4 | 1 | 1 | 2 | 21
FOC control board | 3 | 2 | 3 | 3 | 3 | 27
Full system | 1 | 1 | 4 | 2 | 4 | 18

Affordable Manipulator With FPGA-driven FOC - Field Oriented Control implementation

According to this ranking method, the Full system looks like the best option. This option is very cost efficient as the packages contain motors at an acceptable price. The ease of plug and play allows for quick integration with few problems. The biggest drawback of this option is the limitation of not being able to customize the solution. However, by selecting the right system this should not be an issue. The arm has a set requirements list (comes in a single version), which means the FOC solution does not need to be customized for multiple variants of the arm. Therefore tune-ability and configurability are not needed for this arm.

5.5.VI.Recommended solution
In this case, the full system was selected to be the best option. STMicroelectronics sells FOC kits that fit the requirements. After selecting the full system, a list of requirements in terms of power, size and torque was laid against the offerings found at STMicroelectronics. These kits are full standalone FOC drive systems that fit both the power requirements and precisions requirements of the arm. An affordable FOC was found at STMicroelectronics. The full name of the kit is EVALKIT-ROBOT-1. The current recommendation is to utilize this kit as the FOC drive solution for this case. The affordability and ease of implementation in this use case make it the recommendation to be used for the arm.

Affordable Manipulator With FPGA-driven FOC - Simulation

## 6. Simulation

One of the goals of the project was to create a digital twin of the robot and an interface for controlling both the real robot and the digital twin. Both robots also had the requirement of being fully controllable via ROS.

### 6.1. Simulator of choice

For the simulation the Unity platform was chosen as Gazebo ran quite poorly and had rendering problems. So, it was decided to look at other simulation systems and Unity ended up as the final choice. Unity is also a great option as it also gets used a lot in game design and for other programs. It is also a good fit for artificial intelligence. Unity has a nice programming interface for managing objects in the simulation.

An early choice was to try to make all control to still use ROS under the hood. The Graphical User Interface (GUI) would not require any ROS knowledge, but it will still communicate with Unity using ROS topics.

### 6.2. ROS Communication

The first thing to go into for the simulation is the communication between ROS and Unity as all control of the robots will be done over this system.

In order for communication to happen between the Unity simulation and the ROS system there are 2 ways of communicating:

- A native ROS extension that offers direct communication with ROS for Unity or the programming language that Unity uses (C#)
- A communication bridge system that bridges between ROS and a different communication type that can be made to work with Unity

The first option, though available, was a very out of date and not supported library, so in order
to use this, it had to be extensively tested and likely even fixed or rewritten.
For the second option there already is a system build for ROS that allows communication in a different way. Another company also already started to work on implementing this specific system in Unity itself so the communication was for a big part already handled.

So in the end a RosBridge system was used, that exposes the ROS system over a standard web-socket (ROS Org, 2017). For Unity RosSharp was used (ROSSharp, 2019), which is a library created for Unity that uses the RosBridge system for communication with ROS. An overview can be found in Figure 24.

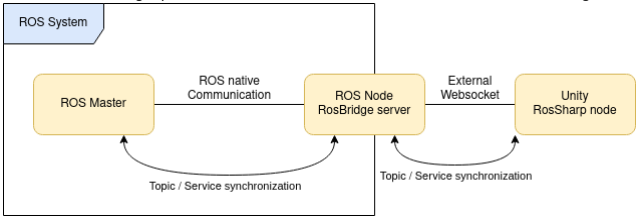
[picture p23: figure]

Figure 24: Architectural overview of the ROS communication structure.

Affordable Manipulator With FPGA-driven FOC - Simulation

For a more in-depth look into the different options and approaches that can be taken and how the possibilities of bridging the ROS communication between the ROS system and Unity were researched (ARMinor 2020 P1, n.d.).

### 6.3. Unity Robot Simulation

As discussed in the ROS Communication section, the simulation is using the RosSharp package from another company to bridge between ROS and Unity (ROSSharp, 2019). This package already has the pub-sub and service/request interfaces working out of the box. Also, most basic message types are included.

One of the more important parts in working with robots in ROS is that that the robot model is shared between the various components that need to drive or take its properties into account. For
the simulation the model itself has to be imported with all the limits etc. To accomplish
this. RosSharp has a built in URDF transfer utility. this way it is very easy to transfer a robot model to Unity. Doing the reverse should also be possible tough this functionality was never used or tested.

Probably the most important feature is being able to read out and control motors or joints.
Readout of the joints was something that was already implemented but had some issues in the reporting that had to be fixed. There are still some issues as there are some issues with the way Unity reports the angles, But it now also has a way of calibrating its zero point.
The writing of the joint states had to be completely rewritten as the implementation
by RosSharp only sets absolute angle values as opposed to controlling the velocity and effort as one would want when simulating actual behavior. The old absolute setting is still available for when one would like to use the system purely as a viewing application where it would mimic exact positions from another robot. This was the way the original system was intended at first.

One of the other parts required for getting joints working was a ROS Controller so that other ROS systems can send commands to the Unity simulation. This was quite a difficult task as documentation was quite sparse on how one would actually needs to implement these controllers.

The last set of functionality that would be needed inside of the Unity simulation is sensors.
The RosSharp library already has sensors for lidar and regular camera’s, other would have to be build when needed. the camera also needs to be redesigned as the current implementation takes to much processing on higher resolutions.

Affordable Manipulator With FPGA-driven FOC - Simulation

### 6.4. The User Interface

The goal of the robot arm is to be an educational substitute to the Universal Robots UR5. Therefore, the user interface is designed to have similar basic functionality to the UR5, namely indicators and controls for each axis, real time robot visualization, moving the end effector linearly, control I/O. Of course, all of that should ideally be used to write a program that can run on the physical robot arm.

The GUI, which is shown in Figure 25, uses the Tkinter Python framework. This framework was chosen as it can work on Windows, Linux and also Raspbian and it also allows freedom into making custom complex widgets. Moreover, the basic widgets available in the framework are intuitive and easy to work with. Tkinter is also supported in python 2, which is the version that is currently used by the most recent ROS release (Melodic) as the time of doing this project. This makes the interface between the UI and ROS simple.

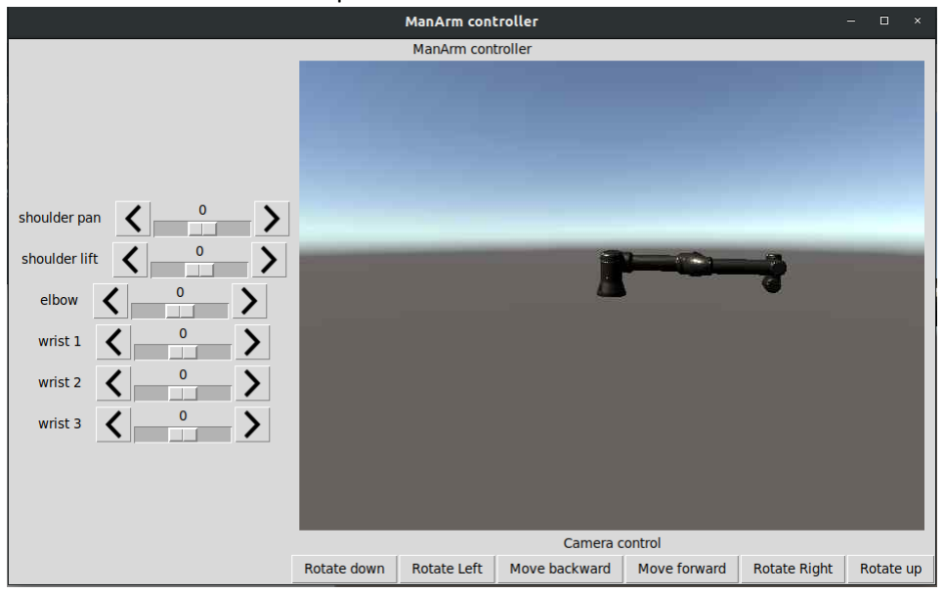
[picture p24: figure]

The GUI’s development is progressing, but as its development started late, it is still in an early stage. Currently the only fully working part is the real time robot visualization. In the GUI there is a live view of the robot’s simulation, in order to visualize the current position and movements of the robot. It was achieved by setting a unity camera to publish compressed images to a ROS topic. The GUI has controls to move the camera around as desired in order to best visualize the robot at all possible poses.

The GUI also has indicators and controls for the axes’ current positions. The axes control is achieved through a ROS topic, which uses the Joy message type. In this way it is possible to have independent control of each individual joint. The indicators still do not work properly. They are correctly converted from radians to degrees, however so far, the current rotation of the arm is not shared from unity to the GUI. In other words, there is no way to tell whether the arm has rotated 90 degrees clockwise or 270 degrees counterclockwise from its reset position. There are also cases where wrong radians are reported to the ROS topic, which also cause wrong values in the GUI.

The other parts of the UI are still under development. After the functionality is done, the GUI would be designed so that it looks good is also useable in different screen resolutions and aspect ratios.

Figure 25: A picture of the GUI. On the left are the joint controls, and on the right the manipulator visuaisation.

Affordable Manipulator With FPGA-driven FOC - Simulation

### 6.5. Future Work

As mentioned before. This system is by no means complete or finished. For the Unity simulation, sensors and joint support will have to be improved. Especially the sensor support has to be looked into so that more types of sensors become available for simulating. At the time of writing this report having full ros_control (the hardware bridge between ros and the robot) and moveit (the movement planning and execution system) support is being finished, but probably could use another revision to make it nicer.

The GUI also has to still be finished, so that it has all the basic features available in the UR5 simulator, moreover the goal is to be able to make a robot program on one system and then save it into a file. This file should later be put in the robot controller in order to execute the program.

A fully featured user-interface that would be compatible with any robot (Unity simulation, real or otherwise) would be a complete project on its own, especially when full scripting and sensor support would be included in it.

Affordable Manipulator With FPGA-driven FOC - Conclusion

## 7. Conclusion

The goal of this project was to design an affordable manipulator arm, with FOC implemented on FPGAs. However, due to the global pandemic, communication and cooperation was made a lot harder, and the project suffered for it. Because of this, the project goal was adapted, and this report now serves to describe the progress that was made, in order to facilitate continuation of this project. Below, a set of recommendations that derive from this project are presented for each project part.

### 7.1. Electrical design

A set of requirements were derived for the electrical design of the affordable manipulator, alongside a list of components that have been selected to comply with the requirements and produce a practical design that can be implemented into the future. This design includes a detailed schematic that connects the different selected components together.

### 7.2. Mechanical design

A basic proof of concept was created for the mechanical design of the arm, complacent with the requirements established. The design could not be finalized due to time constraints; however, a list of hardware was devised. The list is meant to be used in the final design of the robotic arm to be used in conjugation with a list of requirements to produce the visualized design.

### 7.3. FOC implementation

A Field oriented controller was designed and created with the intention to be implemented and used a FPGA board, a MATLAB Simulink model was created with the intention to export the designed controller for FPGA applications. The results are promising, but the tools required for the tuning of the controller were not available at the time of writing. The model successfully was exported as a VHDL file. It proves that, in theory, this is a feasible approach. Due to the constraints of the pandemic and lack of time, the generated file could not be validated, and it is likely to have issues. To compensate for this, alternatives were explored and suggested that would have comparable performance for the project to continue if the generated file approach is deemed to costly or not feasible.

### 7.4. Simulation

The simulation of the robot has been achieved in Unity. This was accomplished using the open source RosSharp package from Siemens to successfully bridge ROS and Unity. The simulation is achieved by the importation of the robot models using URDF files. The control of the arm within the Unity environment, controlling joint speeds as it would be done in reality by rewriting parts of RosSharp. There are issues on join angle reports that are being evaluated and addressed. There is limited functionality with the Sensors that can be used with the Simulation, these being a camera and a lighter.

The proof of concept for a user interface for the control of the robot in this simulation was created, meant to reassemble the Universal Robot Series user interface. It was accomplished through the use Tkinter Python framework to ensure a comfortable array of platforms that should satisfy a broad number of possible users. Currently the GUI has a live visualisation of the robot, and indicators for each axis’ position, but those indicators are inaccurate in edge cases. The GUI is still in development at the time of writing.

Affordable Manipulator With FPGA-driven FOC - Recommendations

## 8. Recommendations

In order to continue the project and improve upon that which has been previously devised and explained, the following recommendations are to be considered. The recommendations are presented per project part.

### 8.1. Electrical design

A circuit board prototype must be built and tested, to validate the schematic design. Then a stress test should be conducted, having the motors run at maximum capacity before suddenly stopping to monitor the stability of the power rails while in operation. Depending on the results of the test, the motor control might have to be adjusted for a more gradual change of speed. Additional capacitors can be added at the base of the robot with the power line is stable, but close to acceptable limits. The board layout is incomplete and requires prototyping and testing. It is recommended to use SMD components as much as possible to keep the board layout compact. The 48V power cables that supply the motors should have a core area of at least 4mm²
to handle the continuous current flow if the motors are constantly in use. The I/O ports for the robotic arm was not addressed in this project, but it is recommended to either use a microcontroller solution or a GPIO I2C controlled expansion board.

### 8.2. Mechanical design

It is recommended to use the suggested joint solutions in the final design of the arm, whilst also exploring into different motors and joint designs for each join to optimize the design. Further consideration must be taken on the final design to account for the fitting of electrical components. It is also recommended to keep in mind the stability of the design at all times.

### 8.3. FOC implementation

The exported VHDL file must be validated, and the PI controllers used within MATLAB Simulink must be tuned. It is recommended to acquire System Identification Toolbox from MathWorks to accomplish this task. From the alternatives explored, it is recommended to use the EVALKIT-ROBOT-1 from STMicroelectronics.

### 8.4. Simulation

The Simulation and GUI show promise in its progress, however, they are still incomplete. Future work is required in the simulation in the form of better sensor support to fully achieve the vision of a digital twin for the imported robot. Further polish will be required in the bridge between ROS and Move-it to unsure a better simulation experience. The GUI is incomplete and still in development, but even after the current proof of concept is realized, another project dedicated to this component will be required to fully achieve the vision desired.

Affordable Manipulator With FPGA-driven FOC - References

## 9. References

ARMinor 2020 P1. (n.d.). ARMinor-2020-Maniputaltor-with-FOC-and-FPGA. Retrieved from GitHub.

Gonçalves, L. (2018). What is SCRUM methodology, everything you need to know. Retrieved from Luis-Goncalves.

igus. (n.d.). igus data sheet robolink D rotary axis asymmetric. igus.

Mathworks. (n.d.). System Identification Toolbox. Retrieved from Mathworks: https://nl.mathworks.com/products/sysid.html

MCP602SN datasheet. (n.d.). Retrieved July 1, 2020, from http://ww1.microchip.com/downloads/en/DeviceDoc/21314g.pdf

Mean Well. (2011, August). RS-35-5 Datasheet. Retrieved July 1, 20, from http://www.farnell.com/datasheets/2286956.pdf

Mean Well. (2019, July 29). RSP-750-48 Datasheet. Retrieved July 2020, 1, from https://static6.arrow.com/aropdfconversion/4d6f3e8da53163c515bb68ac2a8bdc66b79f3d7e/rsp-750-spec.pdf

Performance Motion Devices, Inc. (n.d.). Magellan ® Motion Control IC. Retrieved from Mallegan: https://info.pmdcorp.com/hubfs/Resources/Documentation/Magellan/magellan-motion-control-ic-users-guide.pdf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

RMS. (2017). Mechatronics. Retrieved from RMS Acoustics & Mechatronics.

ROS Org. (2017, October 23). rosbridge_suite. Retrieved from ROS.org: http://wiki.ros.org/rosbridge_suite

ROSSharp. (2019, December 20). ROSSharp -README. Retrieved from GitHub: https://github.com/siemens/ros-sharp/blob/master/README.md

ST. (n.d.). BUZ10 Datasheet. Retrieved July 1, 2020, from https://nl.mouser.com/datasheet/2/389/stmicroelectronics_cd00000673-1204298.pdf

STMicroelectronics. (n.d.). Compact reference design kit for robotics and automation based on STSPIN32F0A. Retrieved from EVALKIT-ROBOT-1 Data brief: https://www.st.com/resource/en/data_brief/evalkit-robot-1.pdf

TI. (n.d.). ADC0820-N datasheet. Retrieved July 1, 2020, from https://www.ti.com/lit/ds/symlink/adc0820-n.pdf?ts=1593611581772

Trinamic. (n.d.). DC Motor Control with TMC4671. Retrieved from Trinamic.com: https://www.trinamic.com/fileadmin/assets/Support/Appnotes/AN025-DC_Motor_Control_with_TMC4671.pdf

Xilinx. (2007, August 21). Spartan 3A development board schematic. Retrieved from https://www.xilinx.com/support/documentation/boards_and_kits/s3astarter_schematic.pdf

Xilinx. (n.d.). Spartan-3A FPGA Family:. Retrieved July 1, 2020, from http://www.farnell.com/datasheets/1911287.pdf

Appendices

# Appendices

Appendices

## Appendix 1: Design requirements

The MoSCoW method was used to draw requirements and assign a priority to the requirements based on the desires and vision of the client. In Table 3 the technical requirements will be listed.

RX = requirement X | MH = Must have | SH = Should Have | NH = Nice to have

Table 3: The table of requirements, split into ROS, Cost, Safety, Size, Production and Design requirements.

Name Requirement | | | Priority
ROS Requirements
R1.1 | Packages for navigation, manipulation and simulation must be provided | MH
R1.2 | The software must approach real time control as much as possible. | MH
Cost Requirements
R2 | The production cost of the arm must be under 1500 EUR in the context for mass | MH
R3.1 | The movement flow of the robot must reasonably smooth, without jittering or mayor vibrations. | MH
R3.2 | The precision of the arm must be within 1mm. | SH
Safety Requirements
R4 | The robot must have an emergency stop system. | MH
Size Requirements
R5.1 | The arm must be less than 710 mm in size (extended arm length). | MH
R5.2 | The arm should be as small as possible. | SH
Production requirements
R6.1 | The arm should be producible with the facilities within Fontys using materials accessible to students. | MH
R6.2 | There should be no visible cables or parts on the finalized design. | MH
R6.3 | The project files must be open source. | MH
Design requirements
R7.1 | The arm must be able to move freely within 6 degrees of freedom. | MH
R7.2 | An FPGA must be used. | MH
R7.3 | The FPGA should control the motors of the arm using field-oriented control. | MH
R7.4 | The implementation of kinematics must be ROS independent. | MH
R7.5 | A raspberry pi4 must be used (with the possibility to upgrade if the need is justified). | MH
R7.6 | Kinematics should be implemented within the low-level hardware. | SH
R7.7 | Brushless DC motors or AC asynchronous must be used for the design and prototyping of the arm. | MH
R7.8 | The arm must be able to carry a payload of 0.200g (excluding the gripper). | MH
R7.9 | The end mount designed must be able to host sensors or end effectors. | MH
R7.10 | The materials used should be a combination of aluminium extrusions, laser cut pieces and 3D printed pieces. | MH
R7.11 | The arm should feature the colour palette of Robohub. | NH

## Appendix 2: Additional FOC subsystems

Appendices

Figure 26: Velocity controller block inside the FOC subsystem.

Figure 27: Current controller block inside FOC subsystem.

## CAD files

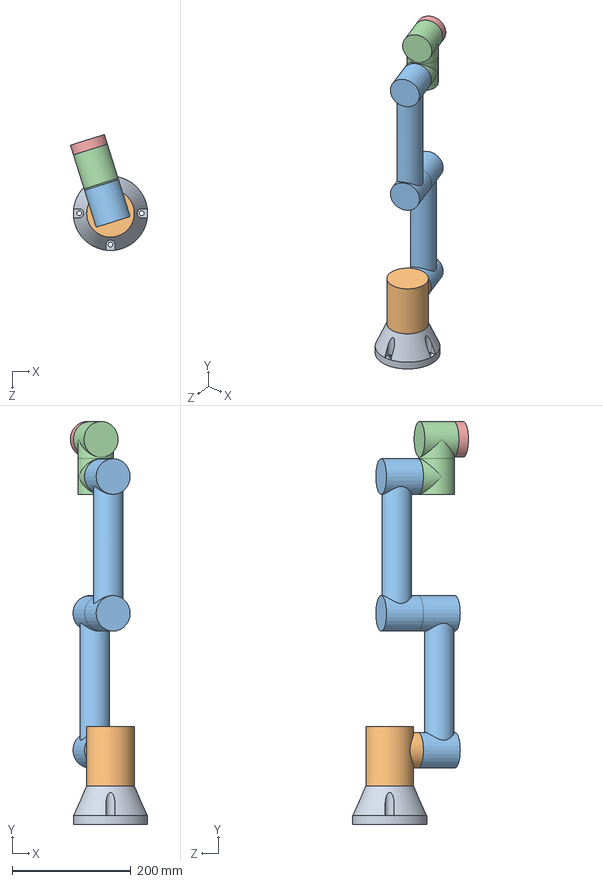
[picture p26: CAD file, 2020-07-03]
Mechanical_Design/Models/armProto.SLDASM
129.9 x 677.5 x 195.0 mm
armBase
armLink1
armLink2 x 2
armLink3 x 2
armEFMount

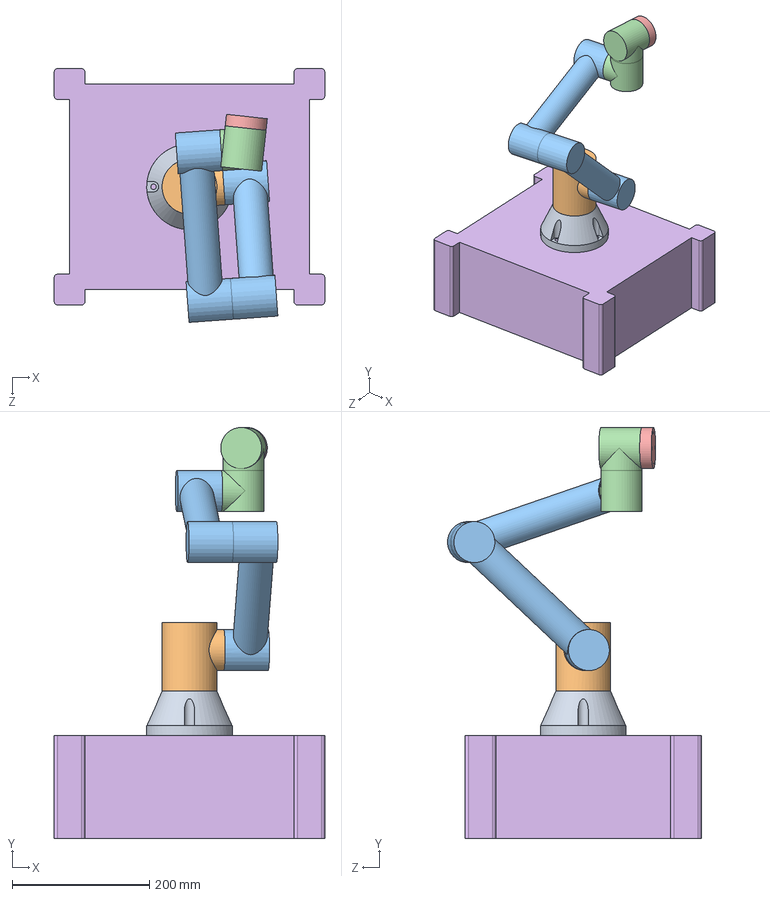
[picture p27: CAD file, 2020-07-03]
Mechanical_Design/Models/Manipulator_model.SLDASM
395.0 x 599.8 x 370.4 mm
armBase
armLink1
armLink2 x 2
armLink3 x 2
armEFMount
Base

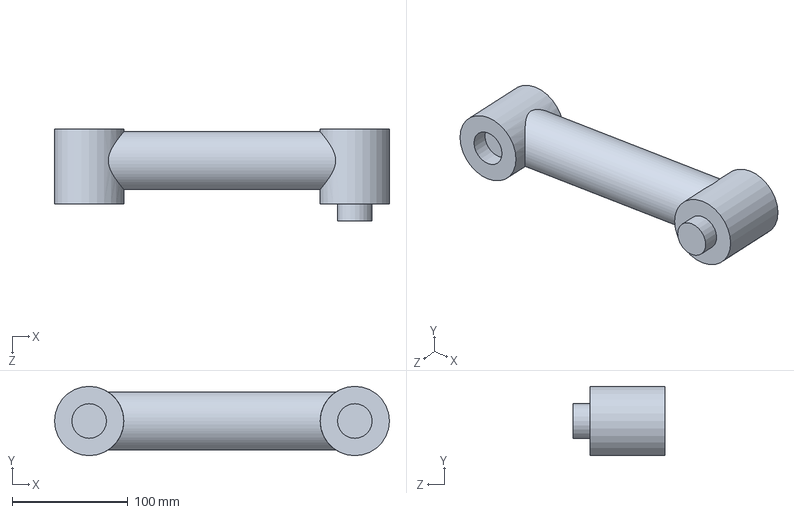
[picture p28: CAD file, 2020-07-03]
Mechanical_Design/Models/Parts/armLink2.SLDPRT
290.0 x 60.0 x 80.0 mm

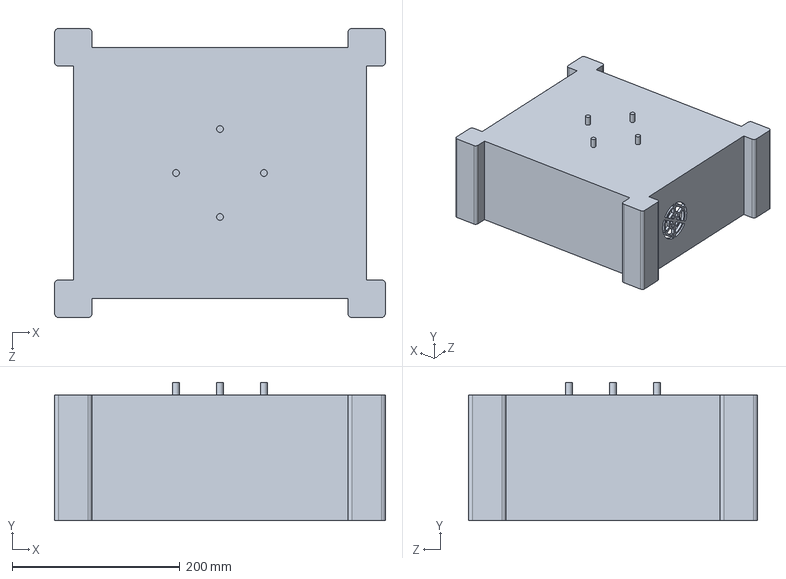
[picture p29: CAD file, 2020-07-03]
Mechanical_Design/Models/Parts/Base.SLDPRT
395.0 x 165.0 x 345.0 mm

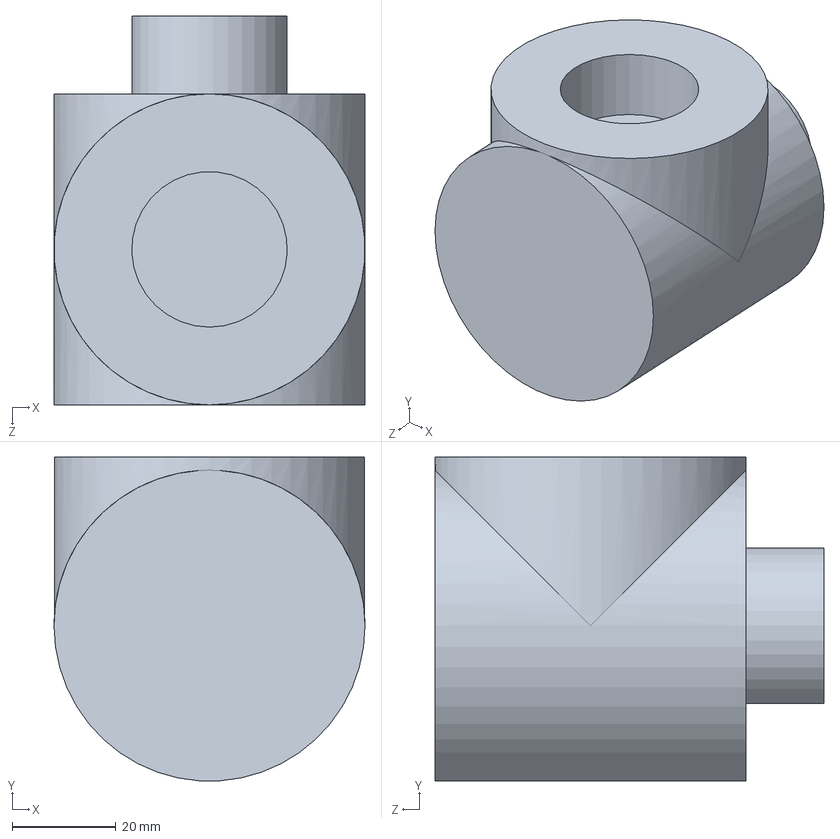
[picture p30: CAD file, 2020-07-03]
Mechanical_Design/Models/Parts/armLink3.SLDPRT
60.0 x 62.4 x 75.0 mm

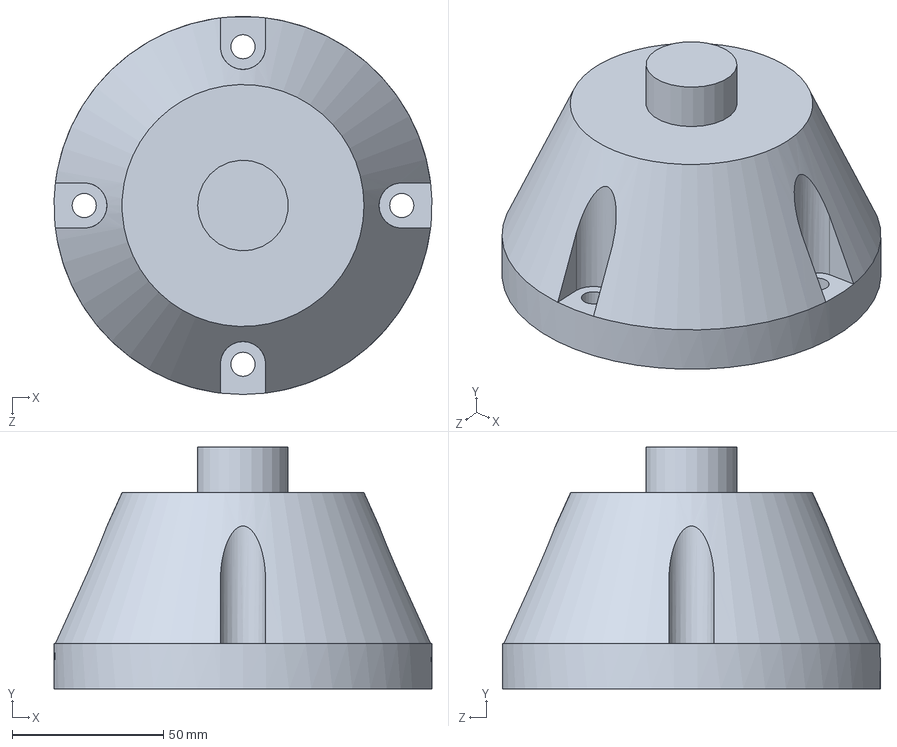
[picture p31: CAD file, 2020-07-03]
Mechanical_Design/Models/Parts/armBase.SLDPRT
124.9 x 80.0 x 125.0 mm

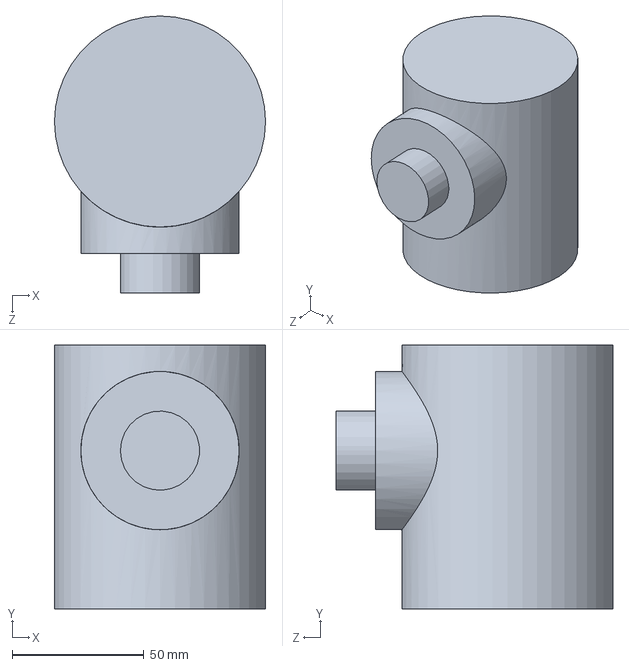
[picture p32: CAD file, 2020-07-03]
Mechanical_Design/Models/Parts/armLink1.SLDPRT
80.0 x 100.0 x 105.0 mm

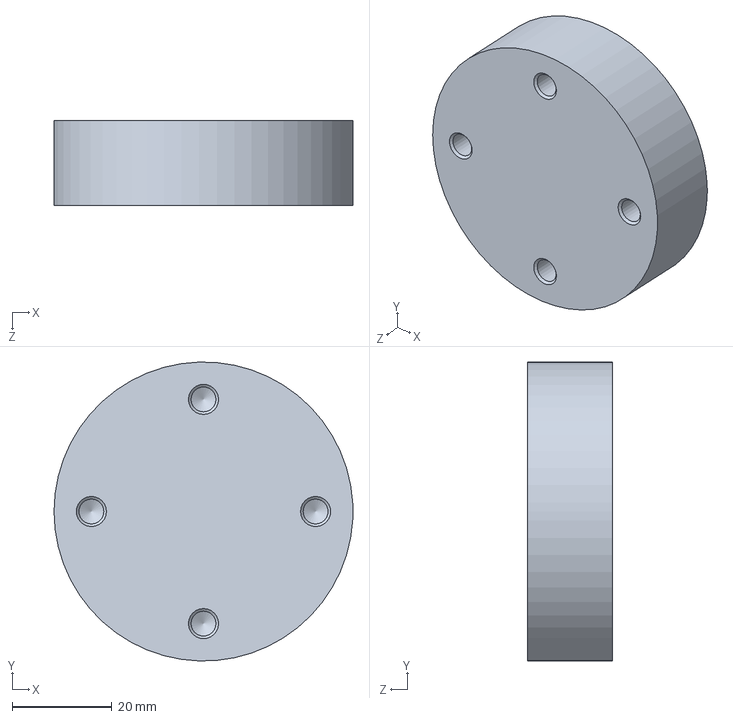
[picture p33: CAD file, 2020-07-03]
Mechanical_Design/Models/Parts/armEFMount.SLDPRT
60.0 x 60.0 x 17.0 mm

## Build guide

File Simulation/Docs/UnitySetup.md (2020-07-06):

Unity Project Setup
======
This document describes how to setup the communication to ROS, how to import robot URDF models and how to connect these to ROS so they can be read out and controlled.

# Project Pre-Requirements (needed packages and scripts)
1. Download and import the `ROS#` package from the asset store (this is the most compatible and best working version). (version 1.6 was used at the time of writing)
2. Download our overrides to the RosSharp asset package ([Simulation/Unity/Assets/RosShap](https://github.com/fontysrobotics/ARMinor-2020-Maniputaltor-with-FOC-and-FPGA/tree/master/Simulation/Unity/Assets/RosSharp)) and copy then over the RosSharp asset package (`<UnityProject>/Assets/RosSharp`)
3. Download and add our additional scripts folder to your assets directory (`<UnityProject>/Assets/`) ([Simulation/Unity/Assets/RosShapFontys](https://github.com/fontysrobotics/ARMinor-2020-Maniputaltor-with-FOC-and-FPGA/tree/master/Simulation/Unity/Assets/RosSharpFontys))

# Project setup
This section covers all setup for importing robot models and setting up communication between ROS and Unity Robots.

## Importing URDF model to Unity
1. Copy the included publish launchfile and change the urdf file to the one you want to use.
2. Start the file_server by running `roslaunch file_server <launchfilename>` (remember the .launch extension needs to be included in the command).
3. In unity open the `RosBridgeClient` menu and click `Transfer URDF from ROS`.
4. When copying form a different project, some settings may retain, like the directory it will try to copy the urdf data to, so reset to defaults when copying rosbridge from other projects.
5. The address is probably `ws://127.0.0.1:9090` unless you changed the port or are connecting over the network.
6. Check the `Asset Path` in the `Settings` is within your project (otherwise things will not work).
7. Click `Read Robot Description` and after downloading let it create the game-objects and your Robot should show up in your simulation.

## Exposing the Robot to ROS and Connecting it to be controlled via ROS
### Initial ROS Bridge setup (the base connection to ROS)
1. Create a new game-object underneath your scene, This object is going to be used to setup the bridge between ROS and Unity (so name it sensibly) (this should not live underneath your robot model, this will be connected later).
2. Add the `Ros Connector` component to this object and configure it correctly like when you imported the model from ROS.  
   The address is probably `ws://127.0.0.1:9090` unless you changed the port or are connecting over the network

### Robot arm joints
1. To each revolute joint (ROS term) / Hinge joint (Unity term) you need to add a `JointStateReader` Component. (this will make it readable for the Joint Publisher later)
2. In each revolute joint (ROS term) / Hinge joint (Unity term) you need to check the joint name in the `Urdf Joint Revolute` component's configuration and how they are expected in ROS, if needed rename them in unity (eg the moveit controller definitions (controller.yaml))
3. Navigate to your RosBridge game-object
4. (optional) create another game-object that is going to be used for setting up the joint state publisher for easy management
5. Add the `Joint State Publisher` component. This will expose the joint states to ROS.  
   In the configuration you should setup the topic as expected by your ROS system (eg. `/joint_states` or `/<robotname>/joint_states`).  
   Under the `Joint State Readers`, set the size to the number of joints, and link each `JointStateReader` to an element.  
   The reference frame might need to be set to world as ROS expects this frame for the origin of the world.
6. TODO Subscribers for arm movement via ROS

### Robot arm calibration
In order to calibrate the arm, by default it will take the initial angle (when starting the simulation) as the 0 point. The axis for each hinge joint is used to correctly denote which way the motor moves.  
There is also the possibility to set a manual calibration in the `JointStateReader` or the `Urdf Joint Revolute` component
//TODO update docs to which of the 2 it is part of as this might change over time it is still TODO

# ROS Setup
When running the simulation the ROSBridge server needs to be running. For most of the systems that interact with the robot, the URDF also needs to be exposed inside of ROS for knowledge about the robot. So when running the simulation you could launch the ROS master with `roslaunch file_server <launchfilename>` (same as when importing the URDF in Unity). Or build your own launch file that launches the RosBridge and exposes the ROBOT URDF file.

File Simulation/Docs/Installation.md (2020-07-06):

Installation
======

## Pre-notes
The unity simulation and ROS system do not strictly have to be running on the same machine.
The Graphical user-interface does require a ROS environment (but is quite easy to setup even without ROS knowledge)

## ROS components
Note: This guide was written for ROS Melodic as the ROS version / distribution. Other version might also work, but you may need to check all packages or substitutes are available for these

### ROS repository packages
the following packages from the ROS repositories are required:
(ROS packages are normally named `ros-${rosversion}-${packagename}` e.g. `ros-melodic-rosbridge-server`)
- rosbridge-server: `rosbridge-server`
  non ROS dependencies: `python-tornado python-bson` (these are not automatically installed so install them manually)
- ros-control: `ros-control ros-controllers`
- moveit: `moveit`

### Other packages
- file_server: [RosSharp github](https://github.com/siemens/ros-sharp/tree/master/ROS/file_server)
  This package allows for full urdf transfer between ROS and Unity
- unity_sim: From this github Repo (Simulation/ROS/unity_sim)
- universal_robot: [universal_robot github](https://github.com/ros-industrial/universal_robot)
  (optional / for the ur5 demo's)

## Unity project setup
All unity simulation setup instructions including setting up a robot and all communications between ROS and Unity are documented in a separate document as this is quite extensive.
See: [Unity Project Setup](UnitySetup.md)

## Graphical User-interface

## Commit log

2020-07-03 add electrical schematics
    adds electrical schematics and libraries for components
    [motor_controller.sch, tool_psu.sch]
2020-07-03 Unity scripts for motor speed control
2020-07-10 RosSharp joint overrides, added motor control and encoder position readout
2020-07-10 Added callibration system to JointStateReader
